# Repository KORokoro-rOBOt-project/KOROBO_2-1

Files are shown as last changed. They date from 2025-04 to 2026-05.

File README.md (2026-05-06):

# 〈第2.1世代〉ころボ / KOROBO (2.1 Gen)
> [!IMPORTANT]
> 組み立て説明を除き、他のデータは最低限完成しました！

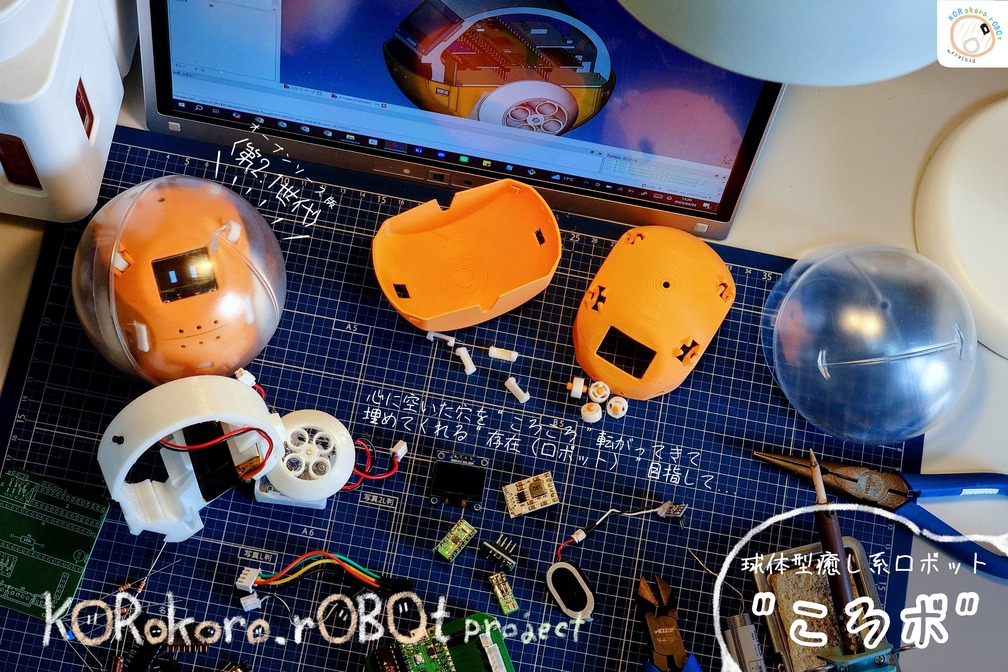
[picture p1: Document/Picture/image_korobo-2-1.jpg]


## 概要 / Overview
### ころボ？
“ころボ” は、カプセルに覆われた手のひらサイズのロボットです。
ただ、表情は四角い2つの瞳、動きはカプセル内で前後左右するも丸いカプセルに振り回され、言葉らしい言葉も話しません。

一見するとポンコツな子ですが、自身や周囲の状況に応じた繊細な反応、設計者の思惑を介さない不完全だからこそ引き出される解釈に、不思議と魅了されます。

そして、ロボットであることをさらけ出してはいるけれど、どこか私たちと同じ気配を感じる新たな存在になってほしいと考えています。

### 第2.1世代
〈第2.1世代〉ころボは、〈第2世代〉のオープンソース版として開発中の子です。
> 私のロボットに対する哲学や目指すべきコンセプトを、より明解にするためのプラットフォームとして考えています。その一方で、多くの方々にも ころボ で多種多様なアプローチをしていただけたらと思っている次第です。

<details>
<summary>第1世代、第2世代 / 1st Gen, 2nd Gen</summary>
	
<table>
  <thead>
    <tr>
      <th align="center"><strong>第1世代 / 1st Gen</strong></th>
      <th align="center"><strong>第2世代 / 2nd Gen</strong></th>
    </tr>
  </thead>
  <tbody>
    <tr>
      <td valign="top">
        〈第1世代〉ころボは、高専の本科生で最後となる高専祭に向けて制作された球体ロボットです。<br><br>
        <strong>直径8</strong> [<strong>cm</strong>]の小さなロボットは、特定の行動パターンを持たず、ランダムに転がります。
        そして、球体という不安定な要素と合わさり、あなたに自由な解釈でロボットと触れ合える余地（
        <a href="https://magazine.serviceology.org/2021/12/20/1433/" target="_blank"><strong>解釈の余地</strong></a>）を与えます。
      </td>
      <td valign="top">
        〈第2世代〉ころボは、
        <a href="https://hacku.yahoo.co.jp/kosen2021/" target="_blank">Hack U KOSEN 2021</a>
        に出場した際に制作した球体ロボットです。
        <strong>直径10</strong> [<strong>cm</strong>]の手にすっぽりおさまるロボットは、周囲の環境（
        <a href="https://twitter.com/KORokororOBOt/status/1652417063770820609" target="_blank"><strong>音</strong></a>、
        明るさ）や自身の状態（
        <a href="https://twitter.com/KORokororOBOt/status/1652271276403347457" target="_blank"><strong>加速度、角速度</strong></a>）を取得します。<br><br>
        それらの情報を反映させたことで、玩具っぽさが軽減され、あなたと同じ世界に住む存在なのだと感じられます。
        また、球体という不安定な要素と合わさり、あなたに自由な解釈でロボットと触れ合える余地（
        <a href="https://magazine.serviceology.org/2021/12/20/1433/" target="_blank"><strong>解釈の余地</strong></a>）を与えます。
      </td>
    </tr>
    <tr>
      <td valign="top">
        &emsp;&emsp;<strong>The first generation</strong> is a spherical robot I created as a department student for the Kosen College Festival.<br><br>
        &emsp;&emsp;The tiny robot, <strong>8 [cm]</strong> in diameter, has no specific action pattern and rolls randomly.
        Combined with the unstable element of the sphere, it gives you room to interact with the robot in any way you like (
        <a href="https://magazine.serviceology.org/2021/12/20/1433/" target="_blank"><strong>Room for Interpretation</strong></a>).
      </td>
      <td valign="top">
        &emsp;&emsp;<strong>The second generation</strong> is a spherical robot created for 
        <a href="https://hacku.yahoo.co.jp/kosen2021/" target="_blank">Hack U KOSEN 2021</a>.
        The <strong>10 [cm]</strong> diameter robot fits snugly in your hand and gets information about its surroundings (
        <a href="https://twitter.com/KORokororOBOt/status/1652417063770820609" target="_blank"><strong>Sound</strong></a>, Luminance) and its state (
        <a href="https://twitter.com/KORokororOBOt/status/1652271276403347457" target="_blank"><strong>Acceleration, Angular Velocity</strong></a>).<br><br>
        &emsp;&emsp;The robot reflects this information, making it feel less like a toy and more like a being that lives in the same world as you.
        Combined with the unstable element of the sphere, it gives you room to interact with the robot in any way you like (
        <a href="https://magazine.serviceology.org/2021/12/20/1433/" target="_blank"><strong>Room for Interpretation</strong></a>).
      </td>
    </tr>
  </tbody>
</table>

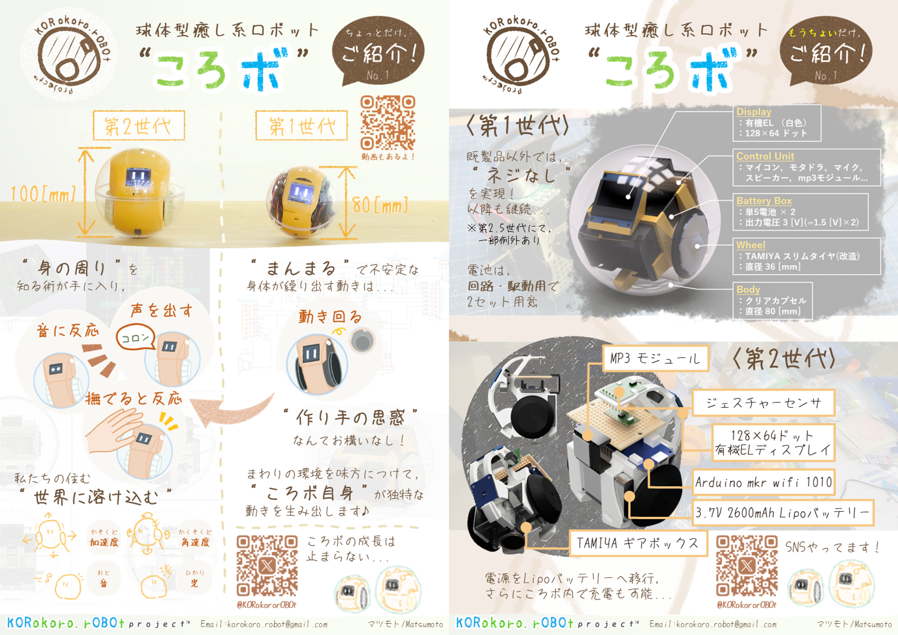
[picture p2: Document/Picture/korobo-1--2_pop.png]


</details>

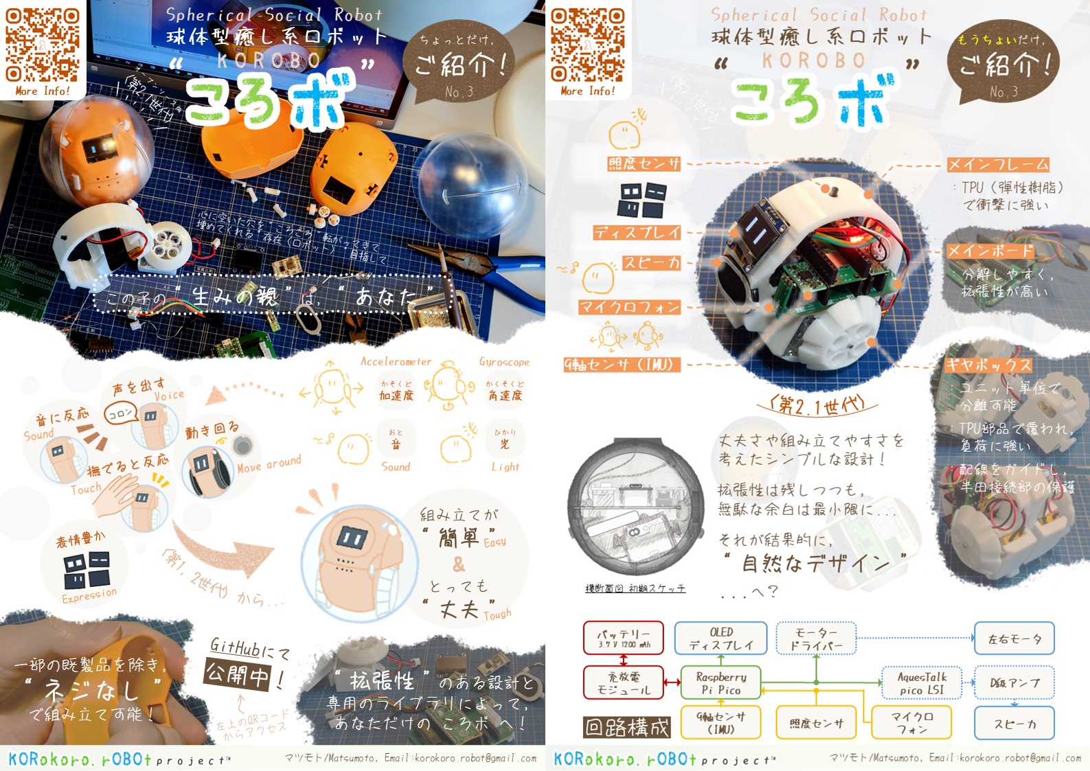
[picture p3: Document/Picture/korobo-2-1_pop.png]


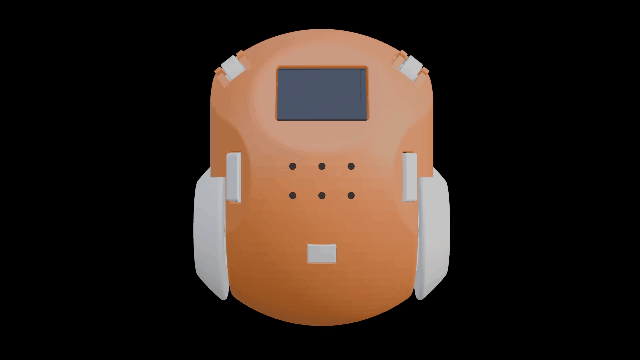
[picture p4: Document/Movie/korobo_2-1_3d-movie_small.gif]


- ころボ 開発当初から大切にしてきた**シンプルな構造**と、**はめ込みによる組み立て方式**[^1]はそのままに、**耐久性**や**拡張性**が向上しました！
    > 机から落ちても、間違えて蹴っ飛ばしても致命傷になることはありません。\
    > マイコンボードとアクセス可能なスペースがあり、思い思いに進化させられます。
[^1]: 既製品のギヤボックスキットは除く。

- マイコンボードに、Raspberry Pi Foundationが提供する[**Raspberry Pi Pico（ラズベリーパイピコ）**](https://www.raspberrypi.com/products/raspberry-pi-pico/)を採用しています！
    > 安価で入手性に優れ、様々な制作事例が存在します。\
    > 多くの互換ボードが存在し、USB端子や用途に合わせて自由に選べます。\
    > <a href="https://www.raspberrypi.com/products/raspberry-pi-pico-2/" >Raspberry Pi Pico 2</a>のように、世代が上がっても互換性があります。
 
## フォルダ構成 / Directory Layout
- [**Board**](Board): 基板発注に必要なガーバーデータ
- [**Code**](Code): ソースコード、ライブラリ
- [**Document**](Document): 調達リスト、画像など
- [**Model**](Model): STEPファイルおよびSTLファイル
## 組み立て / How to Set Up
<details open>
<summary><strong>目次</strong></summary>

0. [部品調達](#01-調達)
1. [駆動ユニット](#10-準備)
2. [配線](#20-準備)
3. [基板](#30-準備)
4. [はめ込み](#40-準備)
5. [ソースコード](#50-準備)
</details>

---
### 0. 部品調達（0/[1](#10-準備)/[2](#20-準備)/[3](#30-準備)/[4](#40-準備)/[5](#50-準備)）
#### 0.1 調達 
[Document](Document)に記載されている各種材料を、添付されているURLの通販サイトや実店舗などにて、調達してください。

#### 0.2 印刷
> [!TIP]
> KORokoro.rOBOt projectの[BOOTH](https://korokoro-robot.booth.pm/items/6812764)にて、**3Dプリンタ製部品**を調達された方は、"[0.3 基板発注 or 作成](#03-基板発注-or-作成)" へ進んでください。
<details>
<summary>手順</summary>

##### 0.20 準備
##### 0.21 PLA
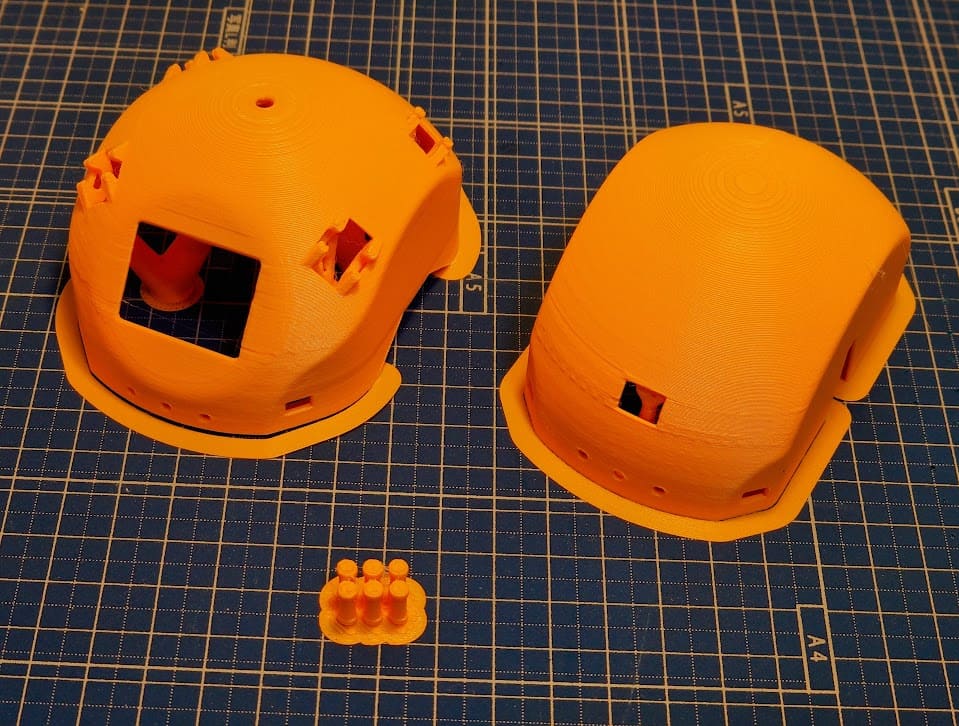
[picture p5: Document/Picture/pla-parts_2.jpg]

<p>
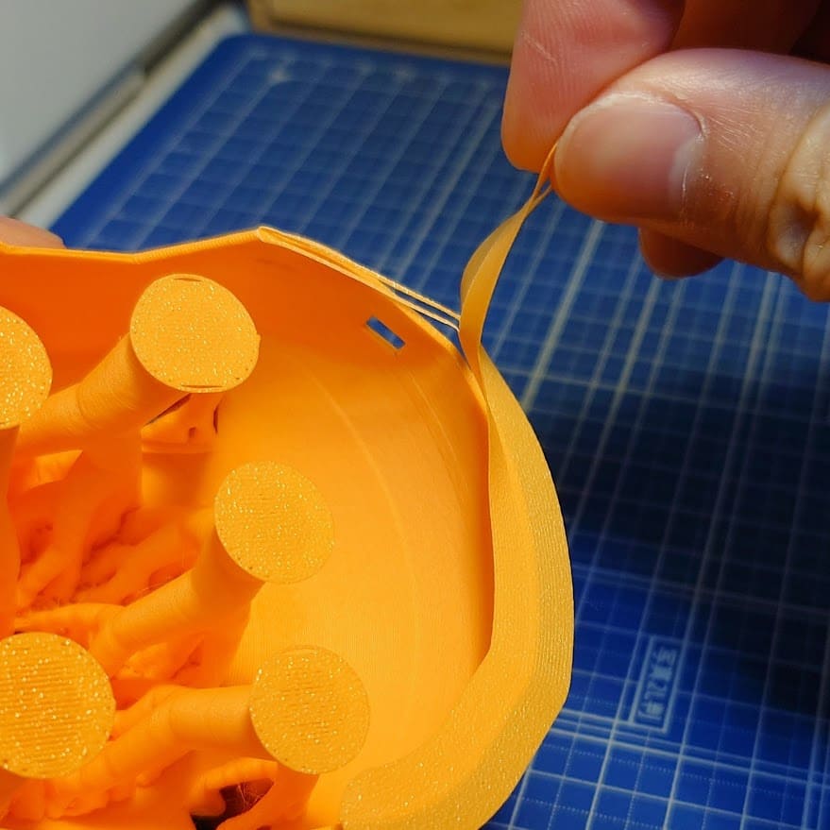
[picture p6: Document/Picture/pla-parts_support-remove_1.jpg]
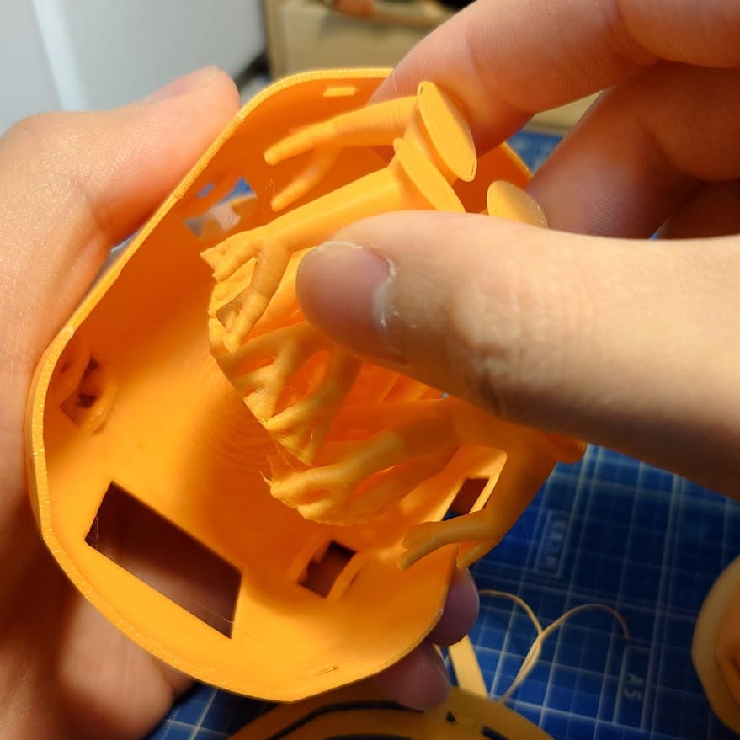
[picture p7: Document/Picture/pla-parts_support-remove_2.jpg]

</p>
<p>
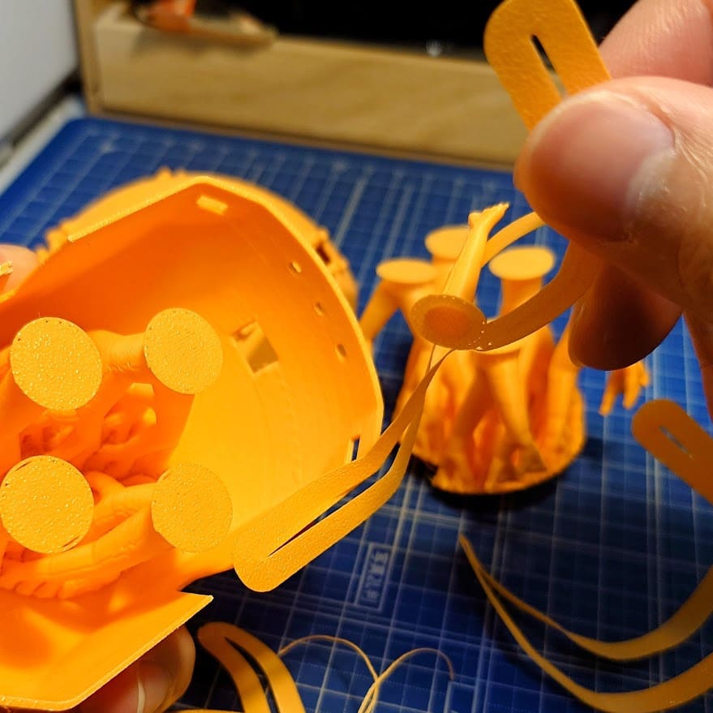
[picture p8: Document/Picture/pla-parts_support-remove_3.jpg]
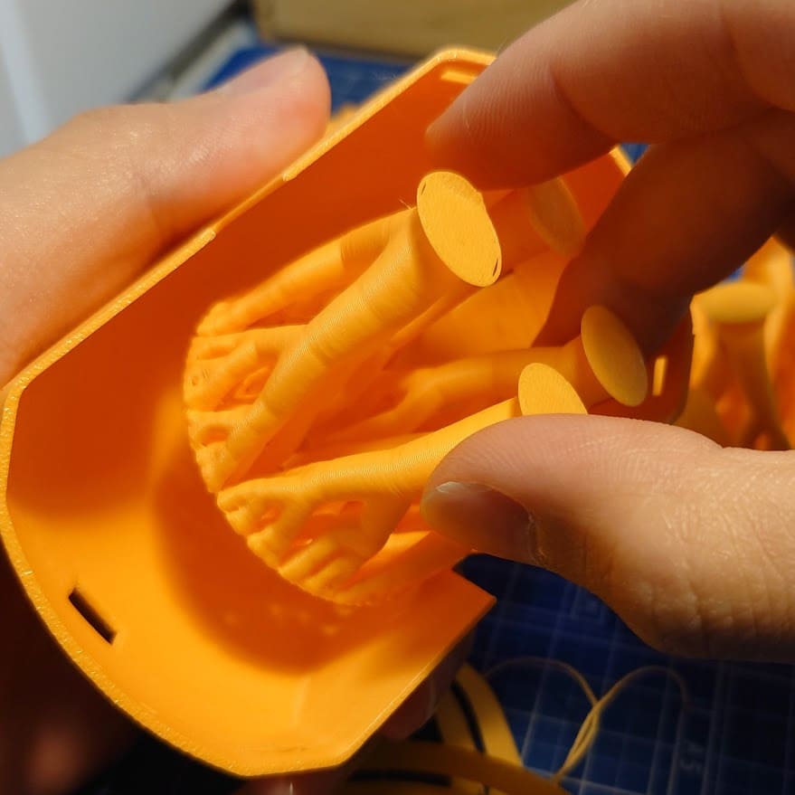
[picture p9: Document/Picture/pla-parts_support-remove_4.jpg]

</p>
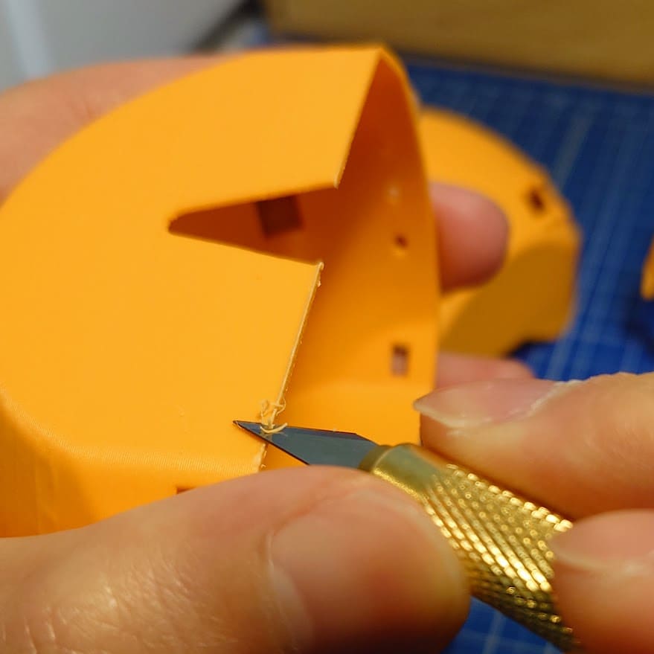
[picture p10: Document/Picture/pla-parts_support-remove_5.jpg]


##### 0.22 TPU
<p>
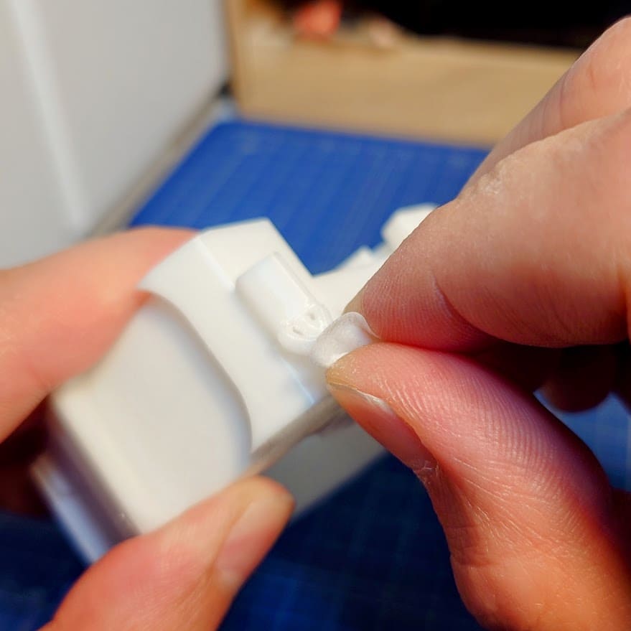
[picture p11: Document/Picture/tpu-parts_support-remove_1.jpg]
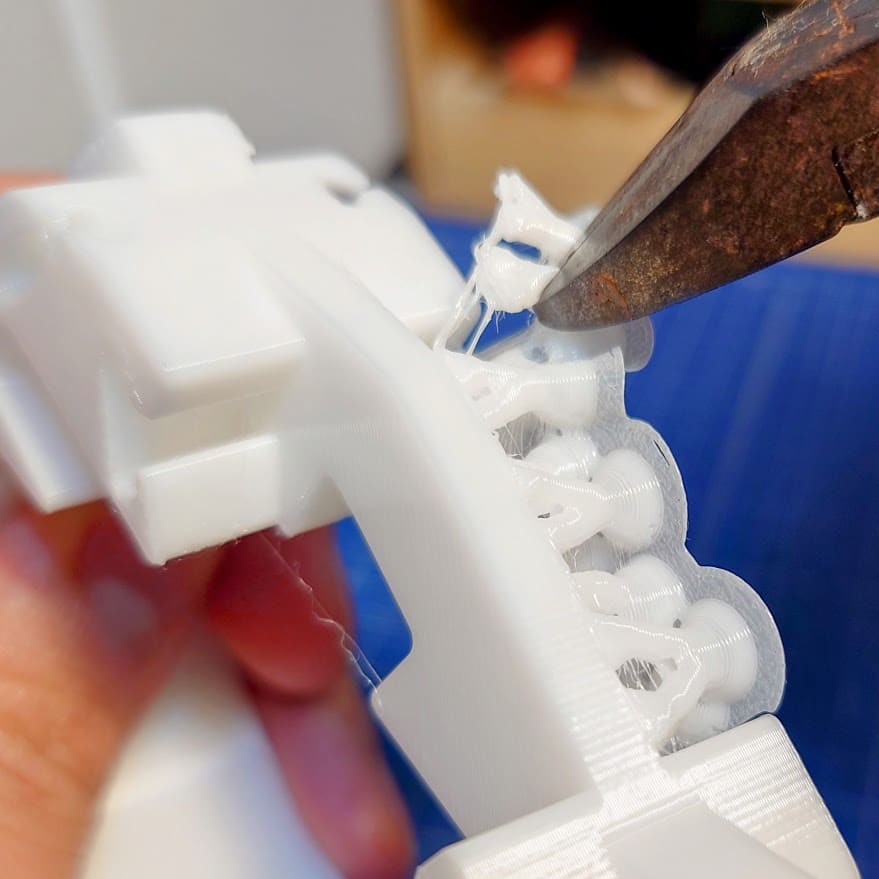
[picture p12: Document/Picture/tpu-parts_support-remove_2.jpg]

</p>
<p>
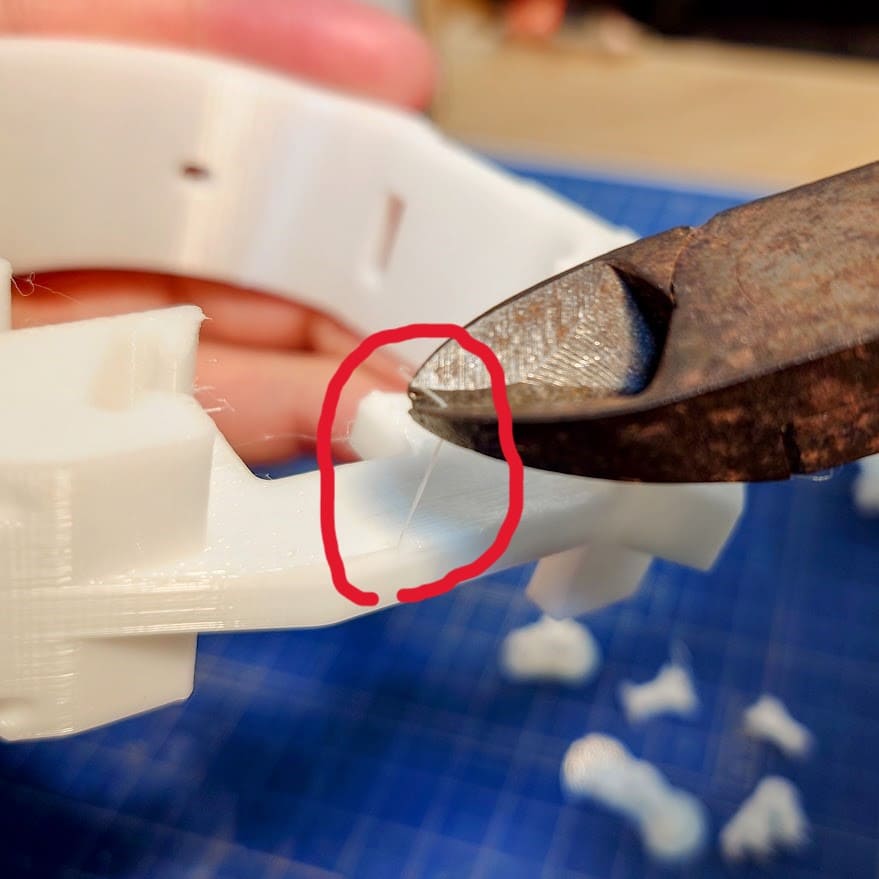
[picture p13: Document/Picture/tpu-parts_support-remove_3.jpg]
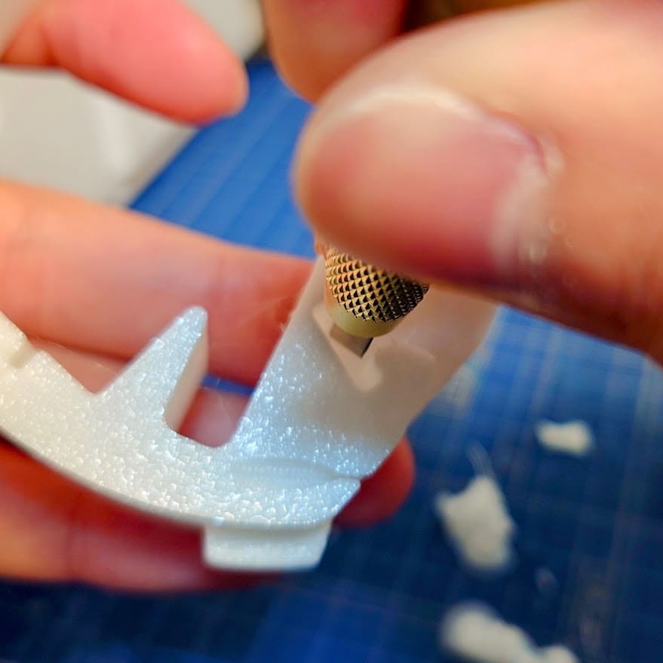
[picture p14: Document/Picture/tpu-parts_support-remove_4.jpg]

</p>
<p>
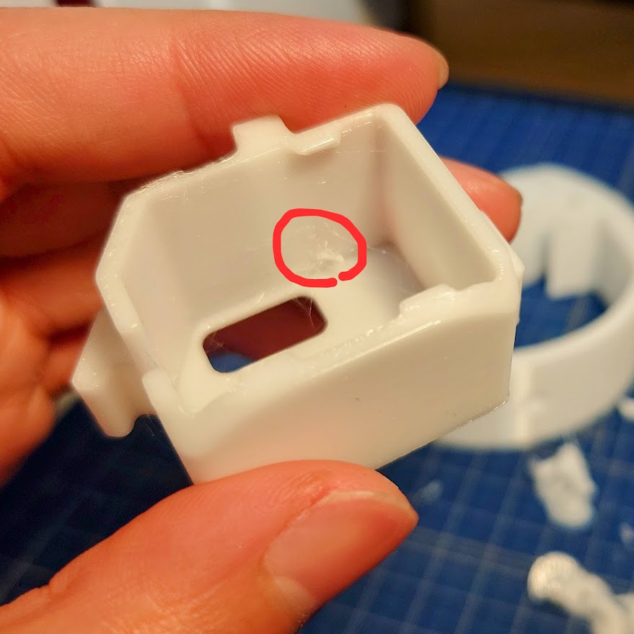
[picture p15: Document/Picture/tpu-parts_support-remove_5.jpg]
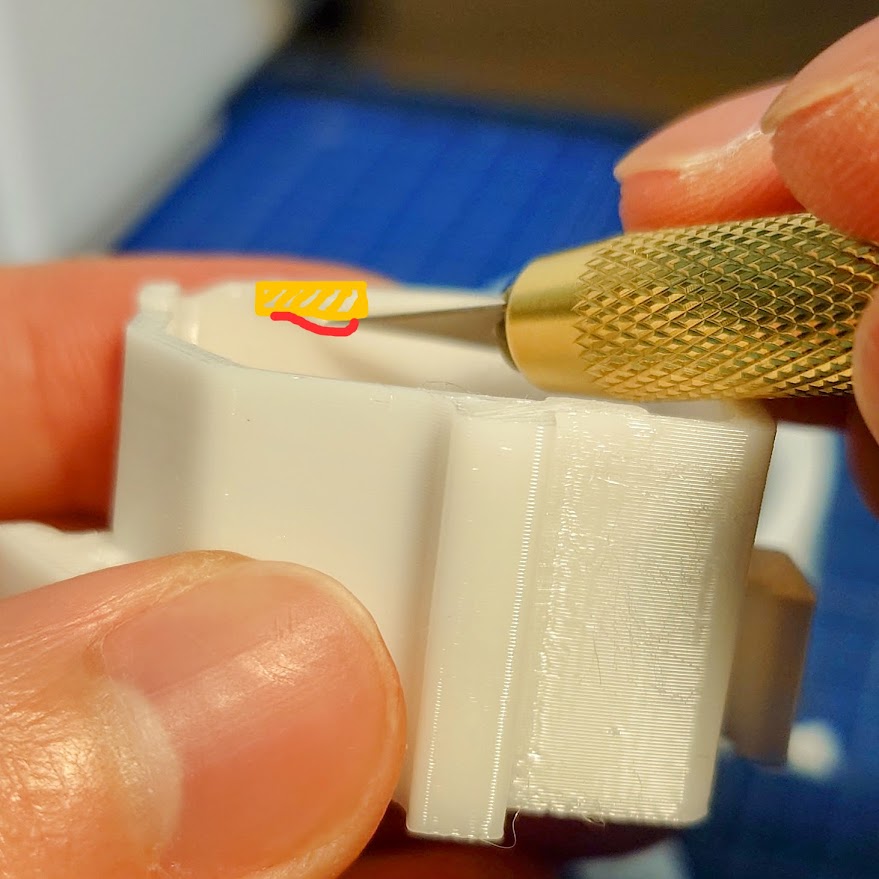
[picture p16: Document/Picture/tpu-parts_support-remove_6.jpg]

</p>
</details>

#### 0.3 基板発注 or 作成
> [!TIP]
> KORokoro.rOBOt projectの[BOOTH](https://korokoro-robot.booth.pm/items/6807081)にて、**メインボード**を調達された方は、"[1. 駆動ユニット](#10-準備)" へ進んでください。
<details open>
<summary>業者に発注される方</summary>

> [**Board**](Board)の中にあるzipファイルをPCBサイトへアップロードしてください。
</details>
<details>
<summary>ユニバーサル基板から作成される方（準備中）</summary>

準備中...
</details>

---
### 1. 駆動ユニット（[0](#01-調達)/1/[2](#20-準備)/[3](#30-準備)/[4](#40-準備)/[5](#50-準備)）
#### 1.0 準備
次の表に示す、工具・部品を準備してください。
<table>
  <thead>
    <tr>
      <th>項目</th>
      <th>名称</th>
      <th>個数</th>
    </tr>
  </thead>
  <tbody>
    <tr>
      <td rowspan="4">工具</td>
      <td>ニッパー</td>
      <td>1</td>
    </tr>
    <tr>
      <td>カッターナイフ or デザインナイフ</td>
      <td>1</td>
    </tr>
    <tr>
      <td>ピンセット</td>
      <td>1</td>
    </tr>
    <tr>
      <td>プラスドライバー</td>
      <td>1</td>
    </tr>
    <tr>
      <td rowspan="4">部品</td>
      <td>タミヤ ミニモーター低速ギヤボックス（4速）</td>
      <td>2</td>
    </tr>
    <tr>
      <td>タミヤ 3mm六角シャフトセット</td>
      <td>1</td>
    </tr>
    <tr>
      <td>メインタイヤ（3Dプリンタ製）</td>
      <td>2</td>
    </tr>
    <tr>
      <td>ギヤボックスカバー（3Dプリンタ製）</td>
      <td>2</td>
    </tr>
  </tbody>
</table>

#### 1.1 ギヤボックス
ミニモーター低速ギヤボックス（4速）を、付属の組み立て説明書に従って、組み立てます。

> [!NOTE]
> - ギヤ比は、"<b>149.9:1</b>" を使用します。
> - 六角シャフトは、3mm六角シャフトセットに付属する "<b>38 [mm]</b>" を使用します。
> - 付属説明書⑥の "<b>L2</b>"、⑦の "<b>クランクプレート</b>" は、使用しません。



#### 1.2 タイヤ＆カバー
> [!NOTE]
> 最後、カプセルに入れる際、圧入度合いの微調整をする必要があります。

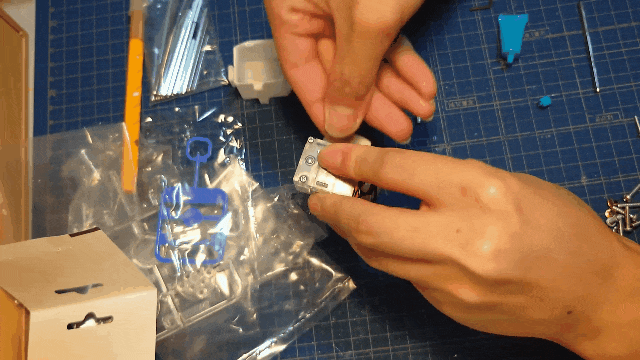
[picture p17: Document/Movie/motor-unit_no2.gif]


1. 調達したメインタイヤを、ギヤボックスのシャフトへ圧入します。

1. 調達したギヤボックスカバーを、ギヤボックスへはめ込みます。

---
### 2. 配線（[0](#01-調達)/[1](#10-準備)/2/[3](#30-準備)/[4](#40-準備)/[5](#50-準備)）
> [!TIP]
> KORokoro.rOBOt projectの[BOOTH](https://korokoro-robot.booth.pm/)にて、**配線類**を調達された方は、"[3. 基板](#30-準備)" へ進んでください。（※現在、準備中）

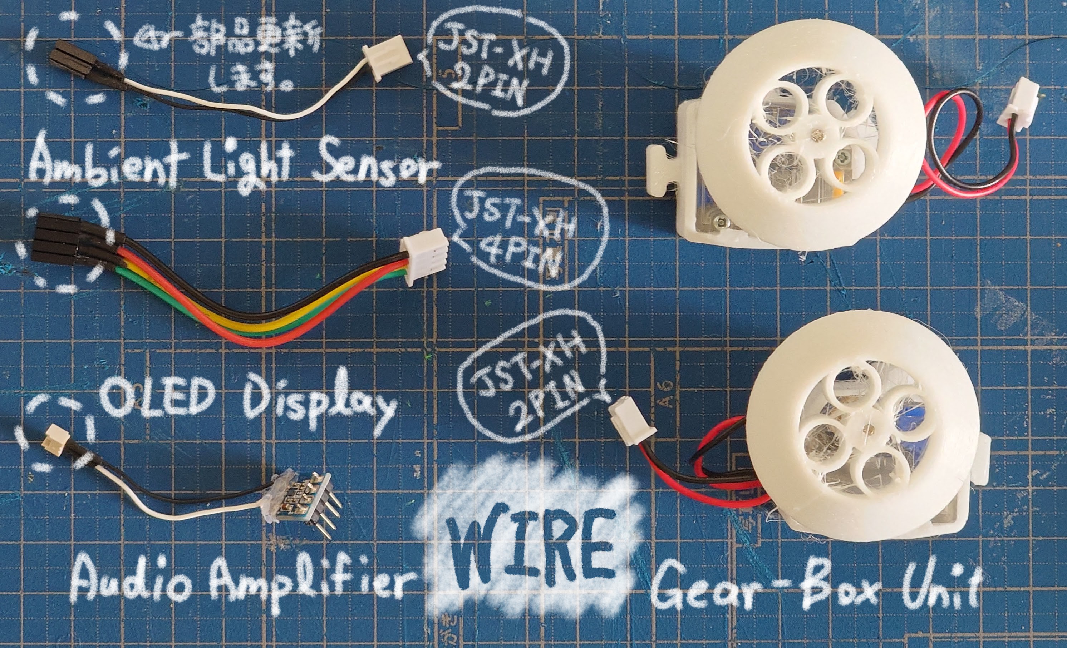
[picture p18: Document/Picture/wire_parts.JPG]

<details open>
<summary>手順</summary>

#### 2.0 準備
次の表に示す、工具・部品を準備してください。

<table>
	<thead>
		<tr>
			<th>項目</th>
			<th>名称</th>
		</tr>
	</thead>
	<tbody>
		<tr>
			<td rowspan="3">工具</td>
			<td>圧着工具</td>
		</tr>
		<tr>
			<td>グルーガン（+ グルースティック）</td>
		</tr>
		<tr>
			<td>ニッパー</td>
		</tr>
		<tr>
			<td rowspan="5">部品</td>
			<td>配線（赤, 黒, 他2色）</td>
		</tr>
		<tr>
			<td>ピンソケット（2P * 1, 4P * 1）</td>
		</tr>
		<tr>
			<td>JST-XH（2P * 3, 4P * 1）</td>
		</tr>
		<tr>
			<td>JST-PH（2P * 1）</td>
		</tr>
		<tr>
			<td>PicoBlade（2P * 1）</td>
		</tr>
	</tbody>
</table>

#### 2.1 駆動ユニット（JST-XH）
> モーター（2P）← 配線（黒、赤）→ JST-XH（2P）

#### 2.2 照度センサ（JST-XH, ピンソケット）
> JST-XH（2P）← 配線（黒、他色*1）→ ピンソケット（2P）

#### 2.3 ディスプレイ（JST-XH, ピンソケット）
> JST-XH（4P）← 配線（黒、赤、他色*2）→ ピンソケット（4P）



#### 2.4 スピーカー（PicoBlade）
> D級アンプ（2P）← 配線（黒、他色*1）→ PicoBlade（2P）

</details>

---
### 3. 基板（[0](#01-調達)/[1](#10-準備)/[2](#20-準備)/3/[4](#40-準備)/[5](#50-準備)）
#### 3.0 準備
次の表・画像に示す、工具・部品を準備してください。

<table>
  <thead>
    <tr>
      <th>項目</th>
      <th>名称</th>
    </tr>
  </thead>
  <tbody>
    <tr>
      <td rowspan="5">工具</td>
      <td>半田こて</td>
    </tr>
    <tr>
      <td>半田</td>
    </tr>
    <tr>
      <td>ニッパー</td>
    </tr>
    <tr>
      <td>机を保護できるマット</td>
    </tr>
    <tr>
      <td>基板や部品を固定できるモノ</td>
    </tr>
  </tbody>
</table>

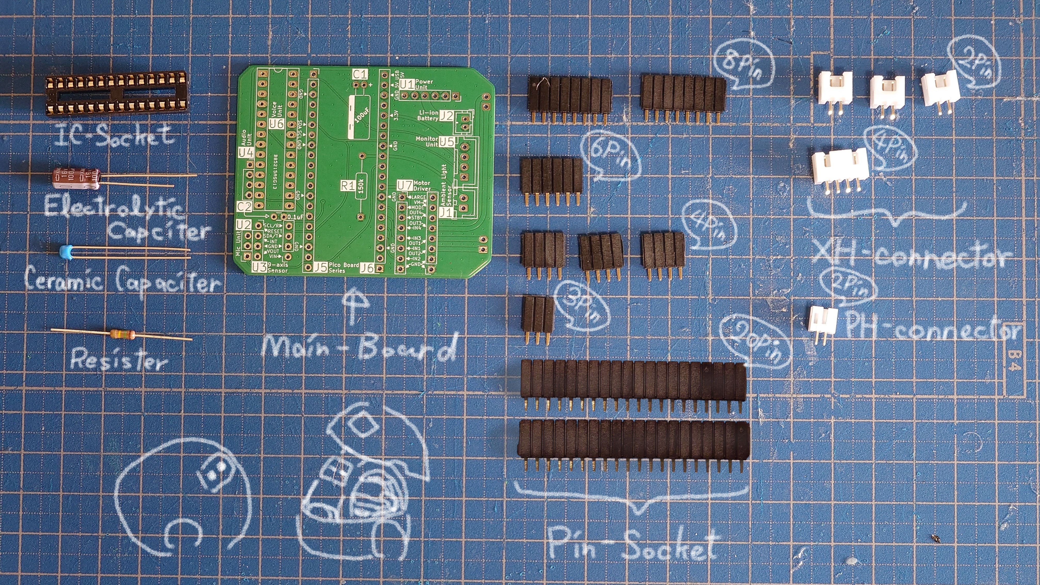
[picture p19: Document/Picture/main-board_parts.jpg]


#### 3.2 半田付け
> [!IMPORTANT]
> モジュール付属のピンヘッダーは、長さが異なるため、別途調達したピンヘッダーを推奨
1. **メインボード**
    > 作業過程ノーカット版 >> [クリック or タップ](https://youtu.be/Ys6NwztTmmA) \
    > 半田付け順：Resister/Capaciter → IC-Socket → XH/PH-Connecter → Pin-Socket

	準備中...
1. **モジュール**\
	準備中...

---
### 4. はめ込み（[0](#01-調達)/[1](#10-準備)/[2](#20-準備)/[3](#30-準備)/4/[5](#50-準備)）

#### 4.0 準備
次の表に示す、工具・部品を準備してください。

<table>
  <thead>
    <tr>
      <th>項目</th>
      <th>名称</th>
    </tr>
  </thead>
  <tbody>
    <tr>
      <td rowspan="3">工具</td>
      <td>やる気に満ちた手</td>
    </tr>
    <tr>
      <td>ビニールテープ</td>
    </tr>
    <tr>
      <td>ハサミ（テープを切断できるもの）</td>
    </tr>
    <tr>
      <td>部品</td>
      <td>これまで準備してきた部品すべて</td>
    </tr>
  </tbody>
</table>

#### 4.1 モジュール（順序あり）
> [!IMPORTANT]
> バッテリには、基板に近い部分をビニールテープなどで数回覆うことが推奨されます。

<div align="center">
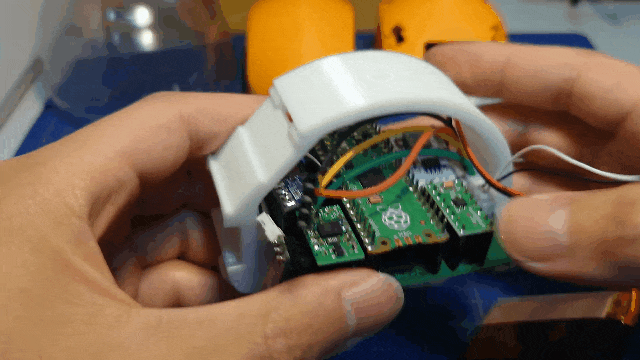
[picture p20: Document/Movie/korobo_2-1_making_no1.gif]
  
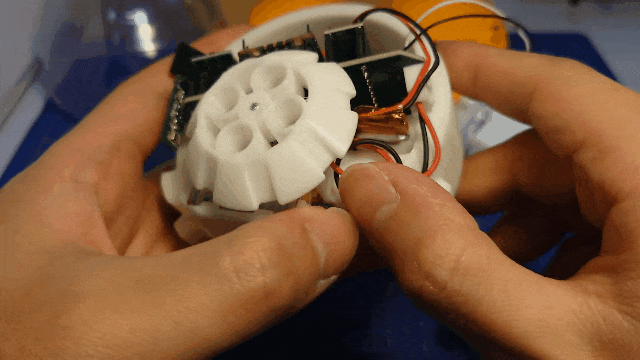
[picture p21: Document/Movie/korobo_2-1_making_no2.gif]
  
</div>

1. 基板 << 配線
1. メインフレーム << 基板（＋配線）
1. メインフレーム << バッテリ
1. メインフレーム << 駆動ユニット

#### 4.2 モジュール（順不同）
> [!NOTE]
> OLEDモジュールと接続するピンソケット（4P）は、接続向きに注意して下さい。GNDピンと黒線がペア！

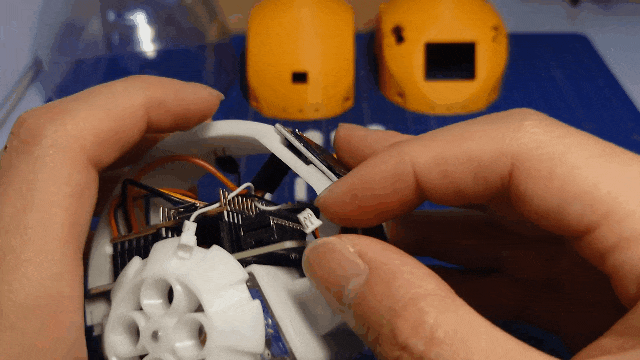
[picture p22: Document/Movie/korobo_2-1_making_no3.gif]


- メインフレーム << OLED、照度センサ、スピーカ

#### 4.3 カバー＆カプセル
<div align="center">
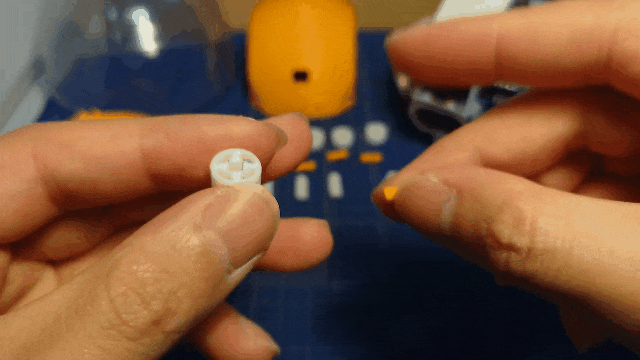
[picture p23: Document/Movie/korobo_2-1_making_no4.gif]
  
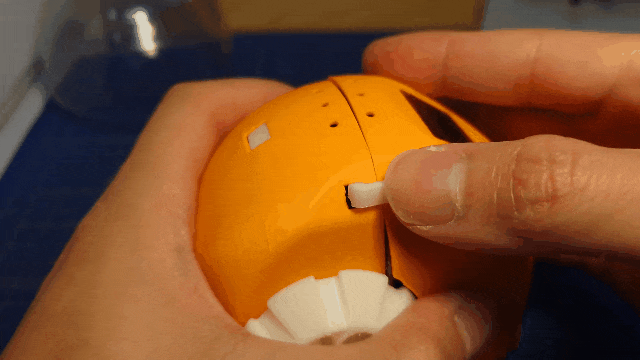
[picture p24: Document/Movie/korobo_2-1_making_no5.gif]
  
</div>

---
### 5. ソースコード（[0](#01-調達)/[1](#10-準備)/[2](#20-準備)/[3](#30-準備)/[4](#40-準備)/5）
#### 5.0 準備
次の表に示す、工具・部品を準備してください。

<table>
  <thead>
    <tr>
      <th>項目</th>
      <th>名称</th>
    </tr>
  </thead>
  <tbody>
    <tr>
      <td rowspan="2">工具</td>
      <td>USBケーブル</td>
    </tr>
    <tr>
      <td>PC</td>
    </tr>
    <tr>
      <td>部品</td>
      <td>ころボ の筐体</td>
    </tr>
  </tbody>
</table>

> [!NOTE]
> USBケーブルは、"PC" と "ころボのマイコンボード" に対応した規格（端子形状）を使用してください。

#### 5.1 配線
準備中...
#### 5.2 書き込み
準備中...
## ころボとの生活 / Life with KOROBO
#### 充電
ころボ の右側面にある、USB差込口に5V出力の**microUSB**を接続する。

#### その他
> [!CAUTION]
> - **リチウムイオン電池**を用いています。取り扱いにはご注意ください。
> - カプセルの仕様上、**完全防水ではありません**。
> - ころボ に関する問題は、自己責任でよろしくお願いいたします。

<p xmlns:cc="http://creativecommons.org/ns#" xmlns:dct="http://purl.org/dc/terms/"><a property="dct:title" rel="cc:attributionURL" href="https://github.com/KORokoro-rOBOt-project/KOROBO_2-1">〈第2.1世代〉ころボ</a> by <a rel="cc:attributionURL dct:creator" property="cc:attributionName" href="https://community.camp-fire.jp/projects/view/764851">KORokoro.rOBOt project</a> is licensed under <a href="https://creativecommons.org/licenses/by-sa/4.0/?ref=chooser-v1" target="_blank" rel="license noopener noreferrer" style="display:inline-block;">Creative Commons Attribution-ShareAlike 4.0 International</a></p>

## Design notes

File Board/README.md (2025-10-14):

# Board
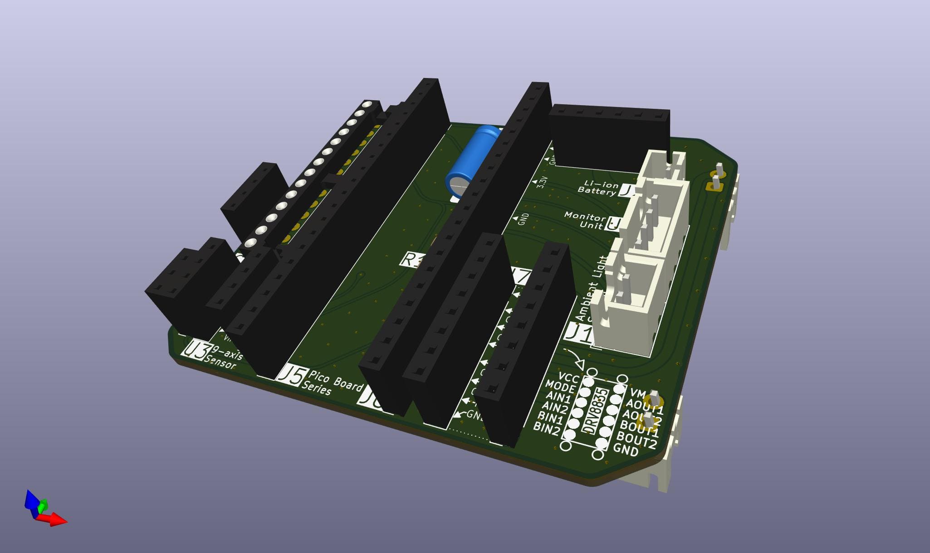
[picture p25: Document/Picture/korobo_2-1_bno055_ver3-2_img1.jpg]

<p>
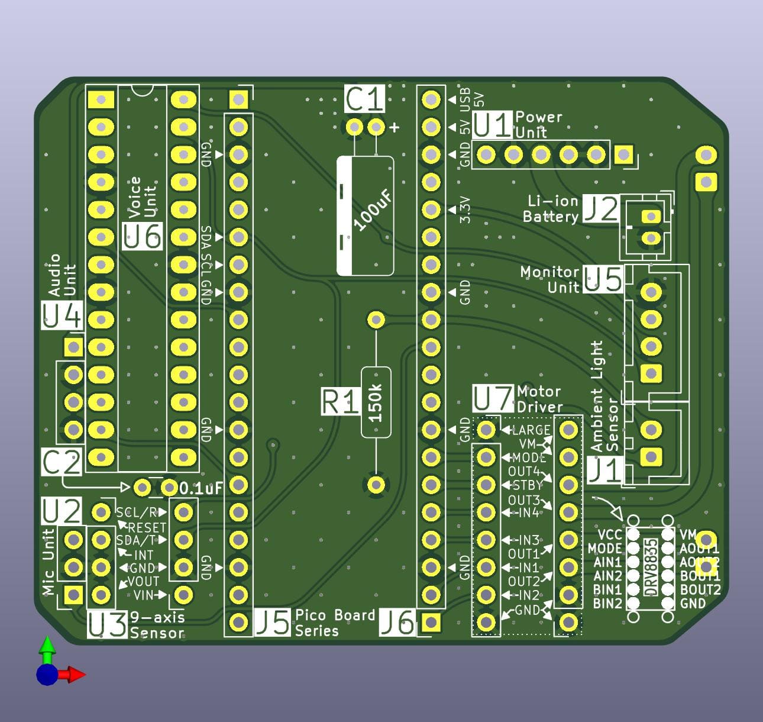
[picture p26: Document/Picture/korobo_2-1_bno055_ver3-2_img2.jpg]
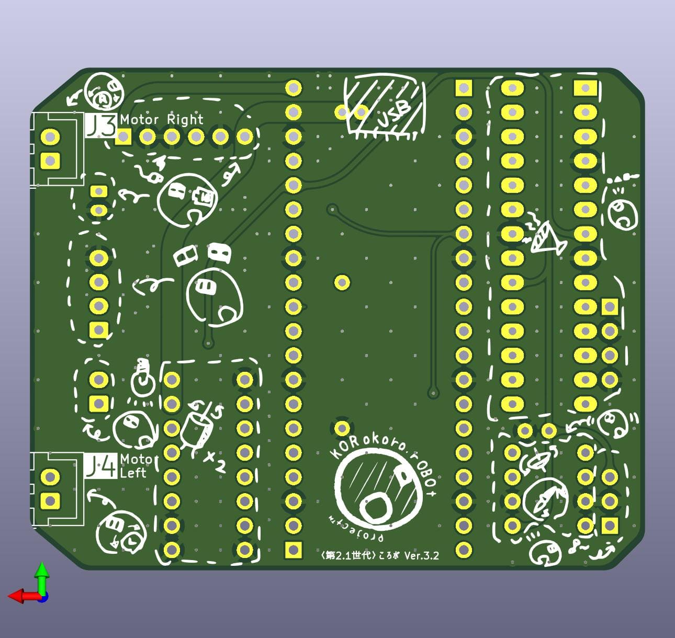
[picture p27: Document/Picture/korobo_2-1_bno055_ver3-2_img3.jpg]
  
</p>
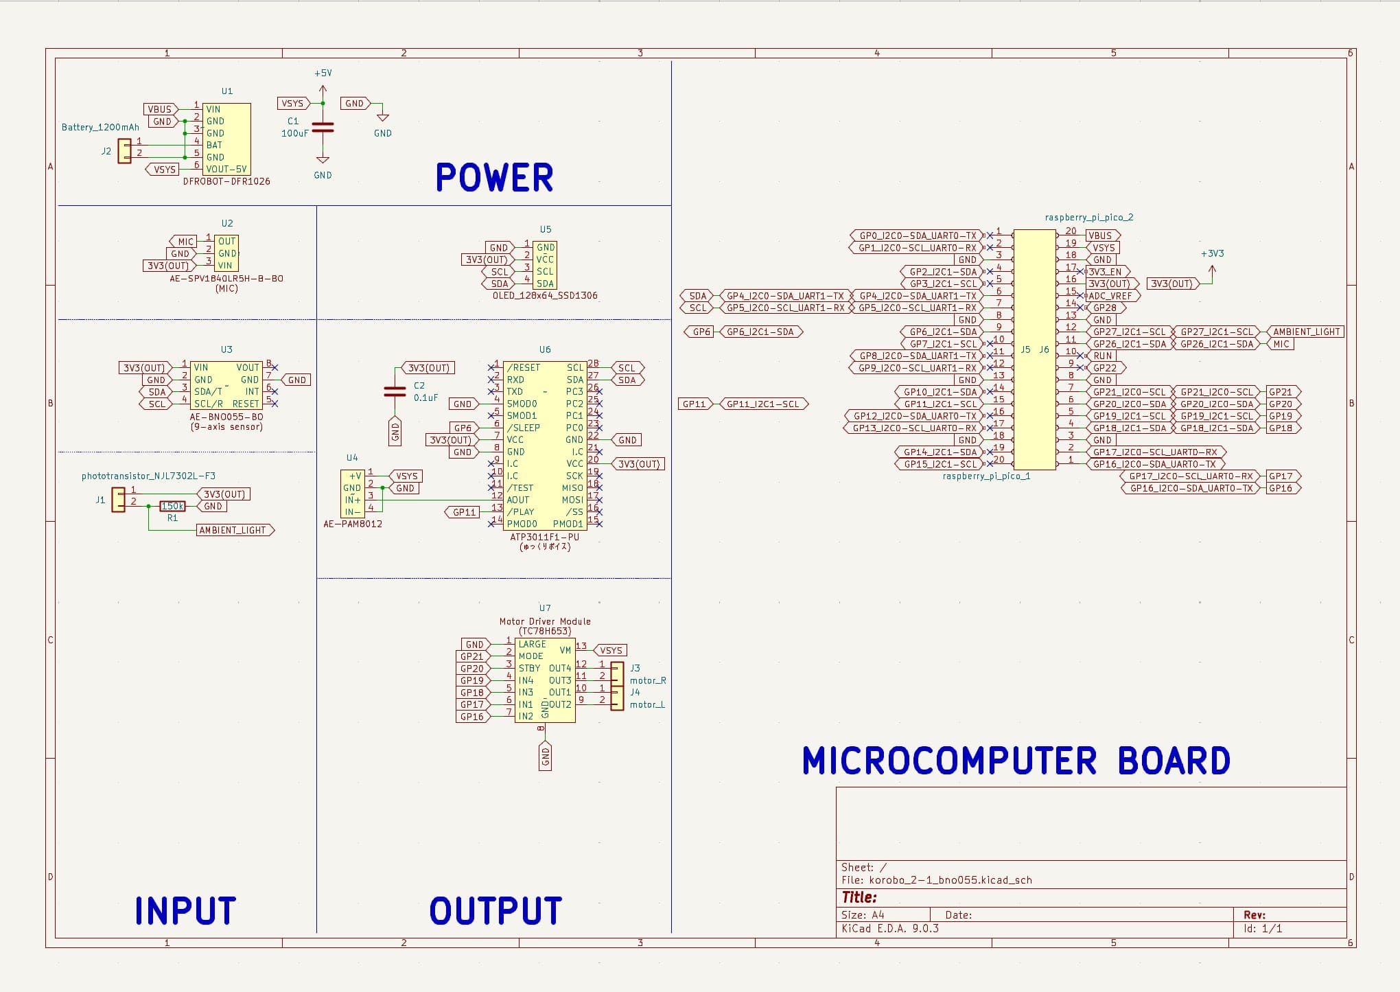
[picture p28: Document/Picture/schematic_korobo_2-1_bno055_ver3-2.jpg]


## 概要 / Overview
〈第2.1世代〉ころボのプリント基板は，組み立てやすさとメンテナンス性に注力しています．

- **ユニバーサル基板（2.54mm）との互換性**
  > プリント基板に設けられたスルーホールのピッチは，すべて2.54mmとなっています．
  > つまり，市販のユニバーサル基板との互換性があるため，プリント基板の調達が困難な方でも作成可能です（理論上...）．

- **ピンソケット・ヘッダーによる接続**
  > メインボードと各種モジュールは，ピンソケットとピンヘッダーによって接続されています．
  > そのため，簡単に取り外しでき，故障時の対応やマイコンボードの載せ替えが柔軟に行えます．

## 部品リスト / Parts List
| ラベル | 仕様 | 個数 | 補足 |
|:---:|---|:----:|---|
| C1 | 100uF | 1 | 電解コンデンサ |
| C2 | 0.1uF | 1 | セラミックコンデンサ |
| J1 | JST XH 2pin | 1 | 照度センサへ接続 |
| J2 | JST PH 2pin | 1 | バッテリへ接続 |
| J3 | JST XH 2pin | 1 | 右モータへ接続 |
| J4 | JST XH 2pin | 1 | 左モータへ接続 |
| J5 | PinSocket 2.54mm 20pin | 1 | マイコンボードへ接続 |
| J6 | PinSocket 2.54mm 20pin | 1 | マイコンボードへ接続 |
| R1 | 150k | 1 | 抵抗 |
| U1 | PinSocket 2.54mm 6pin | 1 | 充放電モジュールへ接続 |
| U2 | PinSocket 2.54mm 3pin | 1 | マイクセンサへ接続 |
| U3 | PinSocket 2.54mm 4pin | 2 | 9軸センサへ接続 |
| U4 | PinSocket 2.54mm 4pin | 1 | D級アンプへ接続 |
| U5 | JST XH 4pin | 1 | OLEDへ接続 |
| U6 | DIP-28 W7.62mm | 1 | ボイスICへ接続 |
| U7 | PinSocket 2.54mm 8pin | 2 | モータドライバへ接続 |



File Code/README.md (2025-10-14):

# Code
> [!NOTE]
> **Arduino IDE**を用いて，書き込みます．ボードマネージャーは，[**arduino-pico**](https://github.com/earlephilhower/arduino-pico)を利用します．

<details>
<summary>書き込み手順（準備中）</summary>
準備中．
</details>

## examples
### mind_2-1
〈第2.1世代〉ころボ の基本プログラム

  <details>
  <summary><ins>ソースコード</ins></summary>
    
  ```cpp
  #include "KoroboLib_2_1.h"
  
  KoroboLib_2_1 korobo;
  
  void setup() {
    // put your setup code here, to run once:
    Serial.begin(9600);
    korobo.begin(TC); // TC: TC78H653, DRV: DRV8833, OLD: main-board ver. 3.1
  }
  
  void loop() {
    // put your main code here, to run repeatedly:
    if (korobo.Sleep(ALL)) {
      korobo.Eye(ALL);
      korobo.Voice(ALL);
      korobo.Move();
    }
  }
  ```
  
  </details>

1. **ライブラリの読み込み**\
    `KoroboLib_2_1 korobo;`の`korobo`の部分は，任意の単語を指定可能．
   ただし，それ以降の`korobo.begin()`のような関数呼び出し時は，指定した単語に変更する必要がある．
    ```cpp
    #include "KoroboLib_2_1.h"
    
    KoroboLib_2_1 korobo;
    ```  
2. **初回処理**\
    
    `korobo.begin()`は，必須．
    ```cpp
    void setup() {
      // put your setup code here, to run once:
      Serial.begin(9600);
      korobo.begin(TC); // TC: TC78H653, DRV: DRV8833, OLD: main-board ver. 3.1
    }
    ```
3. **ループ処理**
    ```cpp
    void loop() {
      // put your main code here, to run repeatedly:
      if (korobo.Sleep(ALL)) {
        korobo.Eye(ALL);
        korobo.Voice(ALL);
        korobo.Move();
      }
    }
    ```

## KoroboLib_2_1
〈第2.1世代〉ころボ を動作させるにあたって必要となるライブラリ

> [!IMPORTANT]
> <b>KoroboLib_2_1</b>は，複数の既存ライブラリに依存しています．
> 事前に，それらのライブラリをインストールしてください[^1][^2][^3][^4]．
> また，各ライブラリには**異なるライセンス**が付与されています．
> これらのライブラリを独自に改変，または ころボ のライブラリへ組み込むといった場合は，十分にご確認ください．
[^1]: https://github.com/adafruit/Adafruit-GFX-Library
[^2]: https://github.com/adafruit/Adafruit_SSD1306
[^3]: https://github.com/adafruit/Adafruit_Sensor
[^4]: https://github.com/adafruit/Adafruit_BNO055

- **`void begin(unsigned int num)`** : 
各モジュールのセットアップ処理関数（[**mind_2-1** / 2. 初回処理](#begin)を参照）．
  > 引数に，搭載しているモータドライバの種類や，メインボードのバージョンを指定することで，互換性を確保している．
  <table>
    <thead>
      <tr>
        <th align="center">unsigned int num = </th>
        <th align="center">対応ボード・モータドライバ</th>
      </tr>
    </thead>
    <tbody>
      <tr>
        <td align="center"><code>TC</code></td>
        <td>メインボード Ver. 3.2，TC78H653 (= 1)</td>
      </tr>
      <tr>
        <td align="center"><code>DRV</code></td>
        <td>メインボード Ver. 3.2，DRV8833 (= 2)</td>
      </tr>
      <tr>
        <td align="center"><code>OLD</code></td>
        <td>メインボード Ver. 3.1，TC78H653 (= 0)</td>
      </tr>
    </tbody>
  </table>

- **`void Imu_getData()`** : 
記述した時点の9軸センサ（加速度・角速度・磁気）の値を取得できる．
  > 1回のループ処理中に複数実行しても，初めに実行した際の値が出力される．
  <table>
    <thead>
      <tr>
        <th align="center"><strong>変数</strong></th>
        <th align="center"><strong>内容</strong></th>
      </tr>
    </thead>
    <tbody>
      <tr>
        <td><code>korobo_acc.x()</code></td>
        <td>加速度（x軸）</td>
      </tr>
      <tr>
        <td><code>korobo_acc.y()</code></td>
        <td>加速度（y軸）</td>
      </tr>
      <tr>
        <td><code>korobo_acc.z()</code></td>
        <td>加速度（z軸）</td>
      </tr>
      <tr>
        <td><code>korobo_gyro.x()</code></td>
        <td>角速度（x軸）</td>
      </tr>
      <tr>
        <td><code>korobo_gyro.y()</code></td>
        <td>角速度（y軸）</td>
      </tr>
      <tr>
        <td><code>korobo_gyro.z()</code></td>
        <td>角速度（z軸）</td>
      </tr>
      <tr>
        <td><code>korobo_mag.x()</code></td>
        <td>磁気（x軸）</td>
      </tr>
      <tr>
        <td><code>korobo_mag.y()</code></td>
        <td>磁気（y軸）</td>
      </tr>
      <tr>
        <td><code>korobo_mag.z()</code></td>
        <td>磁気（z軸）</td>
      </tr>
    </tbody>
  </table>

    <details>
    <summary><ins>使用例</ins></summary>

    ```cpp
    void loop() {
      // put your main code here, to run repeatedly:
      float acc_x, acc_y, acc_z;
      korobo.Imu_getData();
      acc_x = korobo.korobo_acc.x();
      acc_y = korobo.korobo_acc.y();
      acc_z = korobo.korobo_acc.z();
    }
    ```
    </details>

- **`int AmbientLight_getData()`** :
上部光センサの値（0~1023）を取得できる．
- **`int Mic_getData()`** :
マイクセンサの値（0~1023）を取得できる．
- **`void Eye(3-pattern)`**
  
  - 
    ```cpp
    void Eye(unsigned int num)
    ```  
    > 瞳の表示および，瞳が表現する情報を選択できる．
  
    <table>
      <thead>
        <tr>
          <th align="center">unsigned int num = </th>
          <th align="center">内容</th>
        </tr>
      </thead>
      <tbody>
        <tr>
          <td align="center"><code>SOUND</code></td>
          <td>音情報を利用する (= 2)</td>
        </tr>
        <tr>
          <td align="center"><code>IMU</code></td>
          <td>加速度・角速度情報を利用する (= 3)</td>
        </tr>
        <tr>
          <td align="center"><code>LIGHT</code></td>
          <td>光情報を利用する (= 5)</td>
        </tr>
        <tr>
          <td align="center"><code>ALL</code></td>
          <td>すべての情報を利用する (= 30) <b>※推奨</b></td>
        </tr>
      </tbody>
    </table>
    
    <details>
    <summary><ins>使用例</ins></summary>

    ```cpp
    void loop() {
      // put your main code here, to run repeatedly:
      korobo.Eye(SOUND);        // 音情報のみ利用する．（1つの場合）
      korobo.Eye(IMU * LIGHT);  // 加速度・角速度および光情報を利用する．（複数の場合）
      korobo.Eye(ALL);          // すべての情報を利用する．
    }
    ```
    </details>
    
  - 
    ```cpp
    void Eye(int dX_point_u, int dY_point_u, int dX_size_u, int dY_size_u)
    ```
    > 瞳の表示および，瞳の各種パラメータのデフォルト値へ任意の操作を加えられる．
  
    <table>
      <thead>
        <tr>
          <th align="center">変数名</th>
          <th align="center">内容</th>
          <th align="center">値の範囲</th>
        </tr>
      </thead>
      <tbody>
        <tr>
          <td align="center"><code>int dX_point_u</code></td>
          <td>瞳のX座標</td>
          <td align="center">?~?</td>
        </tr>
        <tr>
          <td align="center"><code>int dY_point_u</code></td>
          <td>瞳のY座標</td>
          <td align="center">?~?</td>
        </tr>
        <tr>
          <td align="center"><code>int dX_size_u</code></td>
          <td>瞳の幅</td>
          <td align="center">?~?</td>
        </tr>
        <tr>
          <td align="center"><code>int dY_size_u</code></td>
          <td>瞳の高さ</td>
          <td align="center">?~?</td>
        </tr>
      </tbody>
    </table>
    
  -
    ```cpp
    void Eye(int dX_point_u, int dY_point_u, int dX_size_u, int dY_size_u, unsigned int num)
    ```
    > 上記，2項目の組み合わせ．

- **`void Motor(2-pattern)`** :
左右のモータに任意の操作量を加えられる．

  -
    ```cpp
    void Motor(int motor_power_l, int motor_power_r)
    ```
    > マイコンボードにUSB接続時は，モータ停止とする．<br>
    > 操作量が50以下のとき，ギヤボックスは出力が小さくカプセル内で止まってしまう．<br>
    > そのため，操作量が0~50のきとは，0と同じ扱いとしている．
    
    <table>
      <thead>
        <tr>
          <th align="center">変数</th>
          <th align="center">内容</th>
          <th align="center">値の範囲</th>
        </tr>
      </thead>
      <tbody>
        <tr>
          <td align="center"><code>int motor_power_l</code></td>
          <td>左モータの操作量</td>
          <td align="center">0 ~ 255</td>
        </tr>
        <tr>
          <td align="center"><code>int motor_power_r</code></td>
          <td>右モータの操作量</td>
          <td align="center">0 ~ 255</td>
        </tr>
      </tbody>
    </table>

  -
    ```cpp
    void Motor(int motor_power_l, int motor_power_r, bool flug)
    ```
    > `void Motor(int motor_power_l, int motor_power_r)`における，USB接続時のモータ停止を無効（`flug = false`）とする．

- **`void Move()`** : 
デフォルトの行動関数．
x, y軸の加速度を利用し，姿勢を水平な状態へ維持するようタイヤが動く．
  > この挙動とユーザーによる任意の操作を，同時行えるようにする予定．
- **`boolean Voice_state()`** : 
ころボが発話可能な状態か確認できる．
- **`void Voice_send(char Talk[20])`** : 
任意の文字列を発話できる．
文字列の文法は，[AquesTalk pico LSI](https://www.a-quest.com/products/aquestalkpicolsi.html)のデータシートを参照．
  > <code>Voice_state()</code>を内部に組み込んでいる．
- **`void Voice(unsigned int num)`** : 
デフォルトの発話関数．
発話が表現する情報を選択できる．
  <table>
    <thead>
      <tr>
        <th align="center">unsigned int num = </th>
        <th align="center">内容</th>
      </tr>
    </thead>
    <tbody>
      <tr>
        <td align="center"><code>SOUND</code></td>
        <td>音情報を利用する (= 2)</td>
      </tr>
      <tr>
        <td align="center"><code>IMU</code></td>
        <td>加速度・角速度情報を利用する (= 3)</td>
      </tr>
      <tr>
        <td align="center"><code>LIGHT</code></td>
        <td>光情報を利用する (= 5)</td>
      </tr>
      <tr>
        <td align="center"><code>ALL</code></td>
        <td>すべての情報を利用する (= 30) <b>※推奨</b></td>
      </tr>
    </tbody>
  </table>
  
    <details>
    <summary><ins>使用例</ins></summary>

    ```cpp
    void loop() {
      // put your main code here, to run repeatedly:
      korobo.Voice(SOUND);        // 音情報のみ利用する．（1つの場合）
      korobo.Voice(IMU * LIGHT);  // 加速度・角速度および光情報を利用する．（複数の場合）
      korobo.Voice(ALL);          // すべての情報を利用する．
    }
    ```
    </details>
    
- **（調整中）`boolean Sleep(unsigned int num)`** :
スリープ機能関数．
スリープへ移行する条件の情報を選択できる．
  <table>
    <thead>
      <tr>
        <th align="center">unsigned int num = </th>
        <th align="center">内容</th>
      </tr>
    </thead>
    <tbody>
      <tr>
        <td align="center"><code>SOUND</code></td>
        <td>音情報を利用する (= 2)</td>
      </tr>
      <tr>
        <td align="center"><code>IMU</code></td>
        <td>加速度・角速度情報を利用する (= 3)</td>
      </tr>
      <tr>
        <td align="center"><code>LIGHT</code></td>
        <td>光情報を利用する (= 5)</td>
      </tr>
      <tr>
        <td align="center"><code>ALL</code></td>
        <td>すべての情報を利用する (= 30) <b>※推奨</b></td>
      </tr>
    </tbody>
  </table>
  
    <details>
    <summary><ins>使用例</ins></summary>

    ```cpp
    void loop() {
      // put your main code here, to run repeatedly:
      // 例：Sleep(SOUND), Sleep(IMU * LIGHT)...
      if (korobo.Sleep(ALL)) {
        /* スリープ中に行わない処理... */
      }
      /* スリープ中にも行う処理... */
    }
    ```
    </details>

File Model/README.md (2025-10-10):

# Model
## STL & STEP
> [!NOTE]
> **STEP形式**を推奨しています．

| ファイル名 | 説明 | 印刷数 | 素材 |
|---|---|:---:|:----:|
| [**cover_b_2-1.stl**](STL(OLD)/cover_b_2-1.stl)<br>[**cover_b_2-1.step**](STEP/cover_b_2-1.step) | 本体カバーの下部 | 1 | PLA |
| [**cover_stopper.stl**](STL(OLD)/cover_stopper.stl)<br>[**cover_stopper.step**](STEP/cover_stopper.step) | 本体カバーの上部と下部を繋げるアタッチメント | 4 | TPU |
| [**cover_t_2-1.stl**](STL(OLD)/cover_t_2-1.stl)<br>[**cover_t_2-1.step**](STEP/cover_t_2-1.step.step) | 本体カバーの上部 | 1 | PLA |
| [**main_frame_2-1.stl**](STL(OLD)/main_frame_2-1.stl)<br>[**main_frame_2-1.step**](STEP/main_frame_2-1.step) | メインフレーム | 1 | TPU |
| [**motor_frame_2-1.stl**](STL(OLD)/motor_frame_2-1.stl)<br>[**motor_frame_2-1.step**](STEP/motor_frame_2-1.step) | ギアボックスを包むカバー | 2[^1] | TPU |
| [**wheel_b_2-1.stl**](STL(OLD)/wheel_b_2-1.stl)<br>[**wheel_b_2-1.step**](STEP/wheel_b_2-1.step) | メインタイヤ | 2 | TPU |
| [**wheel_t.stl**](STL(OLD)/wheel_t.stl)<br>[**wheel_t.step**](STEP/wheel_t.step) | 上部滑車 | 4 | TPU |
| [**wheel_t_shaft.stl**](STL(OLD)/wheel_t_shaft.stl)<br>[**wheel_t_shaft.step**](STEP/wheel_t_shaft.step) | 上部滑車の軸 | 4 | PLA |

[^1]: `motor_frame_2-1`は，左右対称で1個ずつ計2個を印刷．

## 2-1Gen_KOROBO.step
各種部品の位置関係などが確認できます．

> [!IMPORTANT]
> 内部データの一部は，[**GRABCAD COMMUNITY**](https://grabcad.com/library)に参加する有志の方々からお借りています[^2][^3]．

[^2]: Raspberry Pi Pico >> https://grabcad.com/library/raspberry-pi-pico-3 
[^3]: Atmega328 >> https://grabcad.com/library/atmega328-1

## korobo_2-1_PLA.3mf & korobo_2-1_TPU.3mf
スライサソフト**Bambu Studio**にて編集したプロジェクトファイルです（設定プリンタ：A1 mini）．

Bambu Lab製品をお持ちの方でしたら，お持ちのプリンタ・フィラメントを選択し，スライスしていただけたらと思います．

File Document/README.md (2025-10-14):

# Document
## [調達リスト / Parts List](Parts-List_KOROBO_2-1.pdf) (2025/9/23)
> [!TIP]
> **電子工作をされている方**は，手元にある部品を確認することで，調達コストを抑えられる場合があります．<br>
> （例：ピンソケット，ピンヘッダ，抵抗，コンデンサなど）

> [!NOTE]
> 一部の部品にて，**組み立てサポート品**を販売しています．<br>
> 「3Dプリンタが家にない」，「基板発注の経験がない」といった方々でも，ころボ に触れ合っていただけます！\
> [▼ 紹介動画（クリック or タップ）](https://www.youtube.com/watch?v=OCpZHEYD810)\
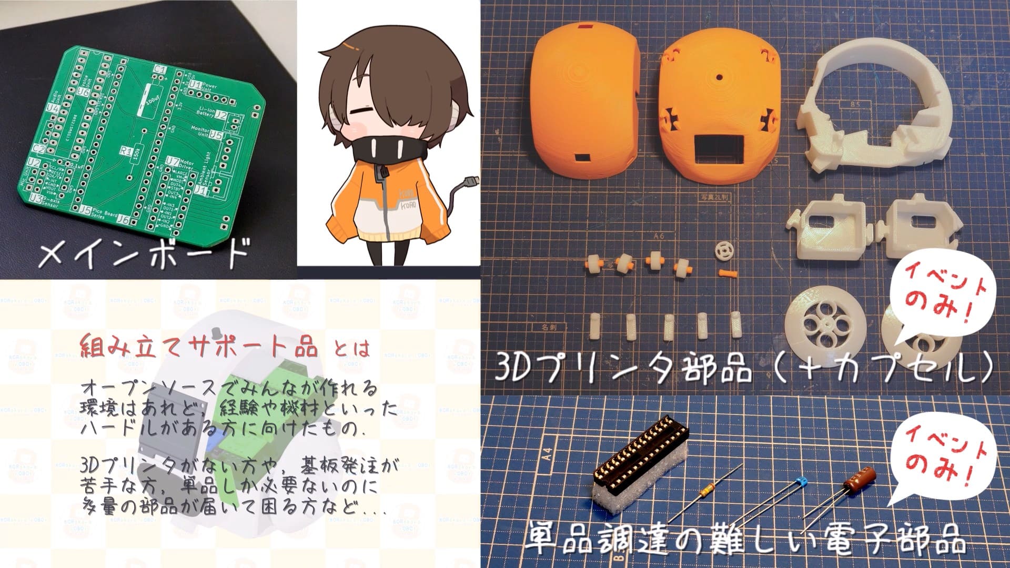
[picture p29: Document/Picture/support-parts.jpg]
> 

> Amazonの商品URLについては，Amazonアソシエイトの短縮リンクを使用しています．<br>
> ※Amazonのアソシエイトとして、KORokoro.rOBOt projectは適格販売により収入を得ています．

### 一覧表示 / All
<details>
<summary>表示 / Preview</summary>
<table>
  <tr>
    <th style="text-align:center;" rowspan="2">No.</th>
    <th style="text-align:center;" rowspan="2">品名</th>
    <th style="text-align:center;">単価</th>
    <th style="text-align:center;" rowspan="2">個数</th>
    <th style="text-align:center;">小計</th>
    <th style="text-align:center;" colspan="2">調達先</th>
    <th style="text-align:center;" rowspan="2">備考</th>
  </tr>
  <tr>
    <th style="text-align:center;">a</th>
    <th style="text-align:center;">a</th>
    <th style="text-align:center;">a</th>
    <th style="text-align:center;">b</th>
  </tr>
  <tr>
    <td colspan="8" align="center">
      <ins>秋月電子</ins>
    </td>
  </tr>
  <tr>
    <td>1</td>
    <td>Raspberry Pi Pico</td>
    <td>¥770</td>
    <td>1</td>
    <td>¥770</td>
    <td><a href="https://akizukidenshi.com/catalog/g/g116132/">秋月電子</a></td>
    <td><a href="https://ssci.to/6900">SWITCH<br>SCIENCE</a></td>
    <td></td>
  </tr>
  <tr>
    <td>2</td>
    <td>0.96インチ 128×64ドット<br>有機ELディスプレイ(OLED) 白色</td>
    <td>¥580</td>
    <td>1</td>
    <td>¥580</td>
    <td><a href="https://akizukidenshi.com/catalog/g/g112031/">秋月電子</a></td>
    <td></td>
    <td></td>
  </tr>
  <tr>
    <td>3</td>
    <td>BNO055使用 9軸センサー<br>フュージョンモジュールキット</td>
    <td>¥2,450</td>
    <td>1</td>
    <td>¥2,450</td>
    <td><a href="https://akizukidenshi.com/catalog/g/g116996/">秋月電子</a></td>
    <td></td>
    <td></td>
  </tr>
  <tr>
    <td>4</td>
    <td>SPV1840LR5H-B使用<br>シリコンマイクモジュールキット</td>
    <td>¥450</td>
    <td>1</td>
    <td>¥450</td>
    <td><a href="https://akizukidenshi.com/catalog/g/g116573/">秋月電子</a></td>
    <td></td>
    <td></td>
  </tr>
  <tr>
    <td>5</td>
    <td>TC78H653FTG<br>モータードライバーモジュール</td>
    <td>¥200</td>
    <td>1</td>
    <td>¥200</td>
    <td><a href="https://akizukidenshi.com/catalog/g/g114746/">秋月電子</a></td>
    <td></td>
    <td></td>
  </tr>
  <tr>
    <td>6</td>
    <td>音声合成LSI ATP3011F1-PU<br>(ゆっくりな女性の音声)</td>
    <td>¥1,050</td>
    <td>1</td>
    <td>¥1,050</td>
    <td><a href="https://akizukidenshi.com/catalog/g/g106220/">秋月電子</a></td>
    <td></td>
    <td></td>
  </tr>
  <tr>
    <td>7</td>
    <td>PAM8012使用2ワット<br>D級アンプモジュール</td>
    <td>¥300</td>
    <td>1</td>
    <td>¥300</td>
    <td><a href="https://akizukidenshi.com/catalog/g/g108217/">秋月電子</a></td>
    <td></td>
    <td></td>
  </tr>
  <tr>
    <td>8</td>
    <td>照度センサー<br>NJL7302L-F3</td>
    <td>¥45</td>
    <td>1</td>
    <td>¥45</td>
    <td><a href="https://akizukidenshi.com/catalog/g/g108910/">秋月電子</a></td>
    <td></td>
    <td></td>
  </tr>
  <tr>
    <td>9</td>
    <td>カーボン抵抗 1/2W150kΩ</td>
    <td>¥100</td>
    <td>1</td>
    <td>¥100</td>
    <td><a href="https://akizukidenshi.com/catalog/g/g107855/">秋月電子</a></td>
    <td></td>
    <td></td>
  </tr>
  <tr>
    <td>10</td>
    <td>積層セラミックコンデンサー<br>0.1μF50V X7R 2.54mm 10個</td>
    <td>¥100</td>
    <td>1</td>
    <td>¥100</td>
    <td><a href="https://akizukidenshi.com/catalog/g/g113582/">秋月電子</a></td>
    <td></td>
    <td></td>
  </tr>
  <tr>
    <td>11</td>
    <td>電解コンデンサー100μ<br>F25V105℃ ルビコンPX</td>
    <td>¥10</td>
    <td>1</td>
    <td>¥10</td>
    <td><a href="https://akizukidenshi.com/catalog/g/g117877/">秋月電子</a></td>
    <td></td>
    <td></td>
  </tr>
  <tr>
    <td>12</td>
    <td>分割ロングピンソケット 1×42 (42P)</td>
    <td>¥80</td>
    <td>3</td>
    <td>¥240</td>
    <td><a href="https://akizukidenshi.com/catalog/g/g105779/">秋月電子</a></td>
    <td></td>
    <td></td>
  </tr>
  <tr>
    <td>13</td>
    <td>ピンヘッダー 1×40 (40P)</td>
    <td>¥35</td>
    <td>3</td>
    <td>¥105</td>
    <td><a href="https://akizukidenshi.com/catalog/g/g100167/">秋月電子</a></td>
    <td></td>
    <td></td>
  </tr>
  <tr>
    <td>14</td>
    <td>ピンソケット 1×20 (20P)<br>リード長10mm</td>
    <td>¥60</td>
    <td>2</td>
    <td>¥120</td>
    <td><a href="https://akizukidenshi.com/catalog/g/g118376/">秋月電子</a></td>
    <td><a href="https://ssci.to/8027">SWITCH<br>SCIENCE</a></td>
    <td></td>
  </tr>
  <tr>
    <td>15</td>
    <td>コネクター用ハウジング 2P</td>
    <td>¥10</td>
    <td>1</td>
    <td>¥10</td>
    <td><a href="https://akizukidenshi.com/catalog/g/g112151">秋月電子</a></td>
    <td></td>
    <td></td>
  </tr>
  <tr>
    <td>16</td>
    <td>コネクター用ハウジング 4P</td>
    <td>&yen;10</td>
    <td>1</td>
    <td>&yen;10</td>
    <td><a href="https://akizukidenshi.com/catalog/g/g112153/">秋月電子</a></td>
    <td><u></u></td>
    <td rowspan="2">
      ピンソケットでも対応できます．<br>
      ▼コネクター側だけ利用する手法もあります．<br>
      <a href="https://eleshop.jp/shop/g/gAAC41C/?srsltid=AfmBOoqFBb0585i-U3NJiWO_EpqYxHgdgGQ-2iUeOSxdOJOnOQ2duirH0ts">共立エレショップ</a>
    </td>
  </tr>
  <tr>
    <td>17</td>
    <td>ケーブル用コネクター 10個</td>
    <td>&yen;50</td>
    <td>1</td>
    <td>&yen;50</td>
    <td><a href="https://akizukidenshi.com/catalog/g/g112160">秋月電子</a></td>
    <td><u></u></td>
    <!-- 備考セルは上の行と結合しているため省略 -->
  </tr>
  <tr>
    <td>18</td>
    <td>ICソケット (28P) スリム300milタイプ</td>
    <td>&yen;280</td>
    <td>1</td>
    <td>&yen;280</td>
    <td><a href="https://akizukidenshi.com/catalog/g/g100013/">秋月電子</a></td>
    <td></td>
    <td></td>
  </tr>
  <tr>
    <td>19</td>
    <td>PHコネクター ベース付ポスト<br>トップ型 2P B2B-PH-K-S</td>
    <td>&yen;10</td>
    <td>1</td>
    <td>&yen;10</td>
    <td><a href="https://akizukidenshi.com/catalog/g/g112802/">秋月電子</a></td>
    <td><a href="https://amzn.to/4nIFLoP">Amazon</a></td>
    <td rowspan="6">候補2のAmazonから調達したほうが，部品を紛失してもある程度予備を確保しつつ，専用ケースで保管できるため，扱いやすいかもです．</td>
  </tr>
  <tr>
    <td>20</td>
    <td>XHコネクター ベース付ポスト<br>トップ型 2P B2B-XH-A(LF)(SN)</td>
    <td>&yen;10</td>
    <td>3</td>
    <td>&yen;30</td>
    <td><a href="https://akizukidenshi.com/catalog/g/g112247/">秋月電子</a></td>
    <td rowspan="5"><a href="https://amzn.to/42ELjbL">Amazon</a></td>
  </tr>
  <tr>
    <td>21</td>
    <td>XHコネクター ベース付ポスト<br>トップ型 4P B4B-XH-A(LF)(SN)</td>
    <td>&yen;10</td>
    <td>1</td>
    <td>&yen;10</td>
    <td><a href="https://akizukidenshi.com/catalog/g/g112249/">秋月電子</a></td>
  </tr>
  <tr>
    <td>22</td>
    <td>XHコネクター ハウジング用コンタクト<br>SXH-001T-P0.6</td>
    <td>&yen;200</td>
    <td>1</td>
    <td>&yen;200</td>
    <td><a href="https://akizukidenshi.com/catalog/g/g112265/">秋月電子</a></td>
  </tr>
  <tr>
    <td>23</td>
    <td>XHコネクター ハウジング 4P XHP-4</td>
    <td>&yen;5</td>
    <td>1</td>
    <td>&yen;5</td>
    <td><a href="https://akizukidenshi.com/catalog/g/g112257/">秋月電子</a></td>
  </tr>
  <tr>
    <td>24</td>
    <td>XHコネクター ハウジング 2P XHP-2</td>
    <td>&yen;5</td>
    <td>3</td>
    <td>&yen;15</td>
    <td><a href="https://akizukidenshi.com/catalog/g/g112255/">秋月電子</a></td>
  </tr>
  <tr>
    <td colspan="8" align="center">
      <ins>marutsu</ins>
    </td>
  </tr>
  <tr>
    <td>25</td>
    <td>コネクタハウジング<br>(2極、ピッチ：1.25mm、1列)</td>
    <td>¥41</td>
    <td>10</td>
    <td>¥410</td>
    <td><a href="https://www.marutsu.co.jp/pc/i/2566668/">marutsu</a></td>
    <td><u></u></td>
    <!-- no.24 と no.25 の備考を結合 -->
    <td rowspan="2">
      No. 25, 26 のどちらかが在庫切れの場合，<br>
      ▼リンク先の商品で代用可能です．<br>
      <a href="https://www.marutsu.co.jp/pc/i/2231331/">代替リンク</a>
    </td>
  </tr>
  <tr>
    <td>26</td>
    <td>1.25mmピッチターミナル【500588000】</td>
    <td>¥9</td>
    <td>4</td>
    <td>¥36</td>
    <td><a href="https://www.marutsu.co.jp/pc/i/584344/">marutsu</a></td>
    <td></td>
    <!-- 備考セルは結合しているため省略 -->
  </tr>
  <tr>
    <td>27</td>
    <td>BATT CHARGER OPEN FRAME 5V 2A<br>【DFR1026】</td>
    <td>&yen;662</td>
    <td>1</td>
    <td>&yen;662</td>
    <td><a href="https://www.marutsu.co.jp/pc/i/43483335/">marutsu</a></td>
    <td><a href="https://www.aitendo.com/product/20089">aitendo</a></td>
    <td></td>
  </tr>
  <tr>
    <td>28</td>
    <td>リチウムイオンポリマー電池<br>(3.7V、1200mAh)【DTP673450(PHR)】</td>
    <td>&yen;2,363</td>
    <td>1</td>
    <td>&yen;2,363</td>
    <td><a href="https://www.marutsu.co.jp/pc/i/1634091/">marutsu</a></td>
    <td></td>
    <td></td>
  </tr>
  <tr>
    <td>29</td>
    <td>ミニモーター低速ギヤボックス(4速)<br>【ITEM70189】</td>
    <td>&yen;946</td>
    <td>2</td>
    <td>&yen;1,892</td>
    <td><a href="https://www.marutsu.co.jp/pc/i/159903/">marutsu</a></td>
    <td><a href="https://amzn.to/3Kh5m9R">Amazon</a></td>
    <td></td>
  </tr>
  <tr>
    <td colspan="8" align="center">
      <ins>Amazon</ins>
    </td>
  </tr>
  <tr>
    <td>30</td>
    <td>3mm六角シャフトセット<br>【ITEM70252】</td>
    <td>&yen;280</td>
    <td>1</td>
    <td>&yen;280</td>
    <td><a href="https://amzn.to/3I9S5iY">Amazon</a></td>
    <td></td>
    <td>38 [mm] 2本を，ギヤボックス付属のシャフトの代わりに使用します．</td>
  </tr>
  <tr>
    <td>31</td>
    <td>PolyTerra PLA 1.75mm径 1000g<br>Sunrise Orange</td>
    <td>&yen;3,278</td>
    <td>1</td>
    <td>&yen;3,278</td>
    <td><a href="https://amzn.to/4gVXI1b">Amazon</a></td>
    <td></td>
    <td rowspan="2">
      約50 [g]ずつ使用<br>
      ▼調達困難な方向けに，印刷物の販売も実施中<br>
      <a href="https://korokoro-robot.booth.pm/items/6812764">https://korokoro-robot.booth.pm/items/6812764</a>
    </td>
  </tr>
  <tr>
    <td>32</td>
    <td>eSUN Flexible TPU 白</td>
    <td>&yen;3,999</td>
    <td>1</td>
    <td>&yen;3,999</td>
    <td><a href="https://amzn.to/46RzRvW">Amazon</a></td>
    <td></td>
    <!-- 備考セルは上の行と結合しているため省略 -->
  </tr>
  <tr>
    <td colspan="8" align="center">
      <ins>その他</ins>
    </td>
  </tr>
  <tr>
    <td>33</td>
    <td>ショートワイヤ付き<br>ミニ楕円形スピーカー（8Ω 1W）</td>
    <td>&yen;486</td>
    <td>1</td>
    <td>&yen;486</td>
    <td><a href="https://ssci.to/5804">SWITCH<br>SCIENCE</a></td>
    <td><a href="https://www.marutsu.co.jp/pc/i/32844060/">marutsu</a></td>
    <td></td>
  </tr>
  <tr>
    <td>34</td>
    <td>収縮チューブ SCG1.0-1B</td>
    <td>&yen;67</td>
    <td>1</td>
    <td>&yen;67</td>
    <td><a href="https://www.monotaro.com/p/1838/1238/?t.q=%94M%88%B3%8Fk">モノタロウ</a></td>
    <td></td>
    <td></td>
  </tr>
  <tr>
    <td>35</td>
    <td>UL1571耐熱架橋ビニル絶縁電線<br>UL1571 AWG30 2m &lt;6&gt;</td>
    <td>&yen;967</td>
    <td>1</td>
    <td>&yen;967</td>
    <td><a href="https://www.monotaro.com/p/4486/8400/?t.q=awg30">モノタロウ</a></td>
    <td></td>
    <td></td>
  </tr>
  <tr>
    <td>36</td>
    <td>100mm空カプセル　10個入り<br>（クリアタイプ）</td>
    <td>&yen;1,155</td>
    <td>1</td>
    <td>&yen;1,155</td>
    <td><a href="https://www.a-muzu.com/category/EMPTY_CAPSULE_008/C0531.html">あミューズ</a></td>
    <td></td>
    <td>1体あたり1個です．．．あと9体</td>
  </tr>
  <tr>
    <td>37</td>
    <td>〈第2.1世代〉ころボ<br>メインボード</td>
    <td>&yen;3,583</td>
    <td>1</td>
    <td>&yen;3,583</td>
    <td>JCBgogo</td>
    <td></td>
    <td>
      基板費用＋輸送費（DHL）から算出．最低5枚から．<br>
      ▼調達困難な方向けに，印刷物の販売も実施中<br>
      <a href="https://korokoro-robot.booth.pm/items/6807081">https://korokoro-robot.booth.pm/items/6807081</a>
    </td>
  </tr>
</table>
</details>

### 3Dプリンタ部品 / Model
<table>
  <tr>
    <th style="text-align:center;" rowspan="2">No.</th>
    <th style="text-align:center;" rowspan="2">品名</th>
    <th style="text-align:center;">単価</th>
    <th style="text-align:center;" rowspan="2">個数</th>
    <th style="text-align:center;">小計</th>
    <th style="text-align:center;" colspan="2">調達先</th>
    <th style="text-align:center;" rowspan="2">備考</th>
  </tr>
  <tr>
    <th style="text-align:center;">a</th>
    <th style="text-align:center;">a</th>
    <th style="text-align:center;">a</th>
    <th style="text-align:center;">b</th>
  </tr>
  <tr>
    <td colspan="8" align="center">
      <ins>3D プリンタ　お持ちの方</ins>
    </td>
  </tr>
  <tr>
    <td>M1_1</td>
    <td>PolyTerra PLA 1.75mm径 1000g<br>Sunrise Orange</td>
    <td>&yen;3,278</td>
    <td>1</td>
    <td>&yen;3,278</td>
    <td><a href="https://amzn.to/4gVXI1b">Amazon</a></td>
    <td></td>
    <td rowspan="2">
      約50 [g]ずつ使用
    </td>
  </tr>
  <tr>
    <td>M2_1</td>
    <td>eSUN Flexible TPU 白</td>
    <td>&yen;3,999</td>
    <td>1</td>
    <td>&yen;3,999</td>
    <td><a href="https://amzn.to/46RzRvW">Amazon</a></td>
    <td></td>
    <!-- 備考セルは上の行と結合しているため省略 -->
  </tr>
  <tr>
    <td colspan="8" align="center">
      <ins>3D プリンタ　お持ちでない方</ins>
    </td>
  </tr>
  <tr>
    <td>M1_2</td>
    <td>組み立てサポート品<br>〈第2.1世代〉ころボ　3Dプリンタ製パーツ</td>
    <td>&yen;2,350</td>
    <td>1</td>
    <td>&yen;2,350</td>
    <td><a href="https://korokoro-robot.booth.pm/items/6812764">BOOTH</a></td>
    <td></td>
    <td>送料別</td>
  </tr>
</table>

### 駆動ユニット / Actuator
<table>
  <tr>
    <th style="text-align:center;" rowspan="2">No.</th>
    <th style="text-align:center;" rowspan="2">品名</th>
    <th style="text-align:center;">単価</th>
    <th style="text-align:center;" rowspan="2">個数</th>
    <th style="text-align:center;">小計</th>
    <th style="text-align:center;" colspan="2">調達先</th>
    <th style="text-align:center;" rowspan="2">備考</th>
  </tr>
  <tr>
    <th style="text-align:center;">a</th>
    <th style="text-align:center;">a</th>
    <th style="text-align:center;">a</th>
    <th style="text-align:center;">b</th>
  </tr>
  <tr>
    <td>A1</td>
    <td>ミニモーター低速ギヤボックス(4速)<br>【ITEM70189】</td>
    <td>&yen;946</td>
    <td>2</td>
    <td>&yen;1,892</td>
    <td><a href="https://www.marutsu.co.jp/pc/i/159903/">marutsu</a></td>
    <td><a href="https://amzn.to/3Kh5m9R">Amazon</a></td>
    <td></td>
  </tr>
  <tr>
    <td>A2</td>
    <td>3mm六角シャフトセット<br>【ITEM70252】</td>
    <td>&yen;280</td>
    <td>1</td>
    <td>&yen;280</td>
    <td><a href="https://amzn.to/3I9S5iY">Amazon</a></td>
    <td></td>
    <td>38 [mm] 2本を，ギヤボックス付属のシャフトの代わりに使用します．</td>
  </tr>
</table>

### メインボード / Board
<table>
  <tr>
    <th style="text-align:center;" rowspan="2">No.</th>
    <th style="text-align:center;" rowspan="2">品名</th>
    <th style="text-align:center;">単価</th>
    <th style="text-align:center;" rowspan="2">個数</th>
    <th style="text-align:center;">小計</th>
    <th style="text-align:center;" colspan="2">調達先</th>
    <th style="text-align:center;" rowspan="2">備考</th>
  </tr>
  <tr>
    <th style="text-align:center;">a</th>
    <th style="text-align:center;">a</th>
    <th style="text-align:center;">a</th>
    <th style="text-align:center;">b</th>
  </tr>
  <tr>
    <td colspan="8" align="center">
      <ins>基板業者へ発注される方</ins>
    </td>
  </tr>
  <tr>
    <td>B1_1</td>
    <td>〈第2.1世代〉ころボ<br>メインボード（基板）</td>
    <td>&yen;3,583</td>
    <td>1</td>
    <td>&yen;3,583</td>
    <td>JCBgogo</td>
    <td></td>
    <td>
      基板費用＋輸送費（DHL）から算出．最低5枚から．<br>
    </td>
  </tr>
  <tr>
    <td colspan="8" align="center">
      <ins>基板完成品を調達される方</ins>
    </td>
  </tr>
  <tr>
    <td>B1_2</td>
    <td>組み立てサポート品<br>〈第2.1世代〉ころボ<br>メインボード（基板）</td>
    <td>&yen;1,000</td>
    <td>1</td>
    <td>&yen;1,000</td>
    <td><a href="https://korokoro-robot.booth.pm/items/6807081">BOOTH</a></td>
    <td></td>
    <td>送料別</td>
  </tr>
  <tr>
    <td colspan="8" align="center">
      <ins>共通</ins>
    </td>
  </tr>
  <tr>
    <td>B2</td>
    <td>Raspberry Pi Pico</td>
    <td>¥770</td>
    <td>1</td>
    <td>¥770</td>
    <td><a href="https://akizukidenshi.com/catalog/g/g116132/">秋月電子</a></td>
    <td><a href="https://ssci.to/6900">SWITCH<br>SCIENCE</a></td>
    <td></td>
  </tr>
  <tr>
    <td>B3</td>
    <td>BNO055使用 9軸センサー<br>フュージョンモジュールキット</td>
    <td>¥2,450</td>
    <td>1</td>
    <td>¥2,450</td>
    <td><a href="https://akizukidenshi.com/catalog/g/g116996/">秋月電子</a></td>
    <td></td>
    <td></td>
  </tr>
  <tr>
    <td>B4</td>
    <td>SPV1840LR5H-B使用<br>シリコンマイクモジュールキット</td>
    <td>¥450</td>
    <td>1</td>
    <td>¥450</td>
    <td><a href="https://akizukidenshi.com/catalog/g/g116573/">秋月電子</a></td>
    <td></td>
    <td></td>
  </tr>
  <tr>
    <td>B5</td>
    <td>TC78H653FTG<br>モータードライバーモジュール</td>
    <td>¥200</td>
    <td>1</td>
    <td>¥200</td>
    <td><a href="https://akizukidenshi.com/catalog/g/g114746/">秋月電子</a></td>
    <td></td>
    <td></td>
  </tr>
  <tr>
    <td>B6</td>
    <td>音声合成LSI ATP3011F1-PU<br>(ゆっくりな女性の音声)</td>
    <td>¥1,050</td>
    <td>1</td>
    <td>¥1,050</td>
    <td><a href="https://akizukidenshi.com/catalog/g/g106220/">秋月電子</a></td>
    <td></td>
    <td></td>
  </tr>
  <tr>
    <td>B7</td>
    <td>PAM8012使用2ワット<br>D級アンプモジュール</td>
    <td>¥300</td>
    <td>1</td>
    <td>¥300</td>
    <td><a href="https://akizukidenshi.com/catalog/g/g108217/">秋月電子</a></td>
    <td></td>
    <td></td>
  </tr>
  <tr>
    <td>B8</td>
    <td>カーボン抵抗 1/2W150kΩ</td>
    <td>¥100</td>
    <td>1</td>
    <td>¥100</td>
    <td><a href="https://akizukidenshi.com/catalog/g/g107855/">秋月電子</a></td>
    <td></td>
    <td></td>
  </tr>
  <tr>
    <td>B9</td>
    <td>積層セラミックコンデンサー<br>0.1μF50V X7R 2.54mm 10個</td>
    <td>¥100</td>
    <td>1</td>
    <td>¥100</td>
    <td><a href="https://akizukidenshi.com/catalog/g/g113582/">秋月電子</a></td>
    <td></td>
    <td></td>
  </tr>
  <tr>
    <td>B10</td>
    <td>電解コンデンサー100μ<br>F25V105℃ ルビコンPX</td>
    <td>¥10</td>
    <td>1</td>
    <td>¥10</td>
    <td><a href="https://akizukidenshi.com/catalog/g/g117877/">秋月電子</a></td>
    <td></td>
    <td></td>
  </tr>
  <tr>
    <td>B11</td>
    <td>分割ロングピンソケット 1×42 (42P)</td>
    <td>¥80</td>
    <td>3</td>
    <td>¥240</td>
    <td><a href="https://akizukidenshi.com/catalog/g/g105779/">秋月電子</a></td>
    <td></td>
    <td></td>
  </tr>
  <tr>
    <td>B12</td>
    <td>ピンヘッダー 1×40 (40P)</td>
    <td>¥35</td>
    <td>3</td>
    <td>¥105</td>
    <td><a href="https://akizukidenshi.com/catalog/g/g100167/">秋月電子</a></td>
    <td></td>
    <td></td>
  </tr>
  <tr>
    <td>B13</td>
    <td>ピンソケット 1×20 (20P)<br>リード長10mm</td>
    <td>¥60</td>
    <td>2</td>
    <td>¥120</td>
    <td><a href="https://akizukidenshi.com/catalog/g/g118376/">秋月電子</a></td>
    <td><a href="https://ssci.to/8027">SWITCH<br>SCIENCE</a></td>
    <td></td>
  </tr>
  <tr>
    <td>B14</td>
    <td>ICソケット (28P) スリム300milタイプ</td>
    <td>&yen;280</td>
    <td>1</td>
    <td>&yen;280</td>
    <td><a href="https://akizukidenshi.com/catalog/g/g100013/">秋月電子</a></td>
    <td></td>
    <td></td>
  </tr>
  <tr>
    <td>B15</td>
    <td>BATT CHARGER OPEN FRAME 5V 2A【DFR1026】</td>
    <td>&yen;662</td>
    <td>1</td>
    <td>&yen;662</td>
    <td><a href="https://www.marutsu.co.jp/pc/i/43483335/">marutsu</a></td>
    <td><a href="https://www.aitendo.com/product/20089">aitendo</a></td>
    <td></td>
  </tr>
</table>

### 配線 / Wire
<table>
  <tr>
    <th style="text-align:center;" rowspan="2">No.</th>
    <th style="text-align:center;" rowspan="2">品名</th>
    <th style="text-align:center;">単価</th>
    <th style="text-align:center;" rowspan="2">個数</th>
    <th style="text-align:center;">小計</th>
    <th style="text-align:center;" colspan="2">調達先</th>
    <th style="text-align:center;" rowspan="2">備考</th>
  </tr>
  <tr>
    <th style="text-align:center;">a</th>
    <th style="text-align:center;">a</th>
    <th style="text-align:center;">a</th>
    <th style="text-align:center;">b</th>
  </tr>
  <tr>
    <td>W1</td>
    <td>コネクター用ハウジング 2P</td>
    <td>¥10</td>
    <td>1</td>
    <td>¥10</td>
    <td><a href="https://akizukidenshi.com/catalog/g/g112151">秋月電子</a></td>
    <td></td>
    <td></td>
  </tr>
  <tr>
    <td>W2</td>
    <td>コネクター用ハウジング 4P</td>
    <td>&yen;10</td>
    <td>1</td>
    <td>&yen;10</td>
    <td><a href="https://akizukidenshi.com/catalog/g/g112153/">秋月電子</a></td>
    <td><u></u></td>
    <td rowspan="2">
      ピンソケットでも対応できます．<br>
      ▼コネクター側だけ利用する手法もあります．<br>
      <a href="https://eleshop.jp/shop/g/gAAC41C/?srsltid=AfmBOoqFBb0585i-U3NJiWO_EpqYxHgdgGQ-2iUeOSxdOJOnOQ2duirH0ts">共立エレショップ</a>
    </td>
  </tr>
  <tr>
    <td>W3</td>
    <td>ケーブル用コネクター 10個</td>
    <td>&yen;50</td>
    <td>1</td>
    <td>&yen;50</td>
    <td><a href="https://akizukidenshi.com/catalog/g/g112160">秋月電子</a></td>
    <td><u></u></td>
    <!-- 備考セルは上の行と結合しているため省略 -->
  </tr>
  <tr>
    <td>W4</td>
    <td>PHコネクター ベース付ポスト<br>トップ型 2P B2B-PH-K-S</td>
    <td>&yen;10</td>
    <td>1</td>
    <td>&yen;10</td>
    <td><a href="https://akizukidenshi.com/catalog/g/g112802/">秋月電子</a></td>
    <td><a href="https://amzn.to/4nIFLoP">Amazon</a></td>
    <td rowspan="6">候補2のAmazonから調達したほうが，部品を紛失してもある程度予備を確保しつつ，専用ケースで保管できるため，扱いやすいかもです．</td>
  </tr>
  <tr>
    <td>W5</td>
    <td>XHコネクター ベース付ポスト<br>トップ型 2P B2B-XH-A(LF)(SN)</td>
    <td>&yen;10</td>
    <td>3</td>
    <td>&yen;30</td>
    <td><a href="https://akizukidenshi.com/catalog/g/g112247/">秋月電子</a></td>
    <td rowspan="5"><a href="https://amzn.to/42ELjbL">Amazon</a></td>
  </tr>
  <tr>
    <td>W6</td>
    <td>XHコネクター ベース付ポスト<br>トップ型 4P B4B-XH-A(LF)(SN)</td>
    <td>&yen;10</td>
    <td>1</td>
    <td>&yen;10</td>
    <td><a href="https://akizukidenshi.com/catalog/g/g112249/">秋月電子</a></td>
  </tr>
  <tr>
    <td>W7</td>
    <td>XHコネクター ハウジング用コンタクト<br>SXH-001T-P0.6</td>
    <td>&yen;200</td>
    <td>1</td>
    <td>&yen;200</td>
    <td><a href="https://akizukidenshi.com/catalog/g/g112265/">秋月電子</a></td>
  </tr>
  <tr>
    <td>W8</td>
    <td>XHコネクター ハウジング 4P XHP-4</td>
    <td>&yen;5</td>
    <td>1</td>
    <td>&yen;5</td>
    <td><a href="https://akizukidenshi.com/catalog/g/g112257/">秋月電子</a></td>
  </tr>
  <tr>
    <td>W9</td>
    <td>XHコネクター ハウジング 2P XHP-2</td>
    <td>&yen;5</td>
    <td>3</td>
    <td>&yen;15</td>
    <td><a href="https://akizukidenshi.com/catalog/g/g112255/">秋月電子</a></td>
  </tr>
  <tr>
    <td>W10</td>
    <td>コネクタハウジング<br>(2極、ピッチ：1.25mm、1列)</td>
    <td>¥41</td>
    <td>10</td>
    <td>¥410</td>
    <td><a href="https://www.marutsu.co.jp/pc/i/2566668/">marutsu</a></td>
    <td><u></u></td>
    <!-- no.24 と no.25 の備考を結合 -->
    <td rowspan="2">
      No. W10, W11 のどちらかが在庫切れの場合，<br>
      ▼リンク先の商品で代用可能です．<br>
      <a href="https://www.marutsu.co.jp/pc/i/2231331/">代替リンク</a>
    </td>
  </tr>
  <tr>
    <td>W11</td>
    <td>1.25mmピッチターミナル【500588000】</td>
    <td>¥9</td>
    <td>4</td>
    <td>¥36</td>
    <td><a href="https://www.marutsu.co.jp/pc/i/584344/">marutsu</a></td>
    <td></td>
    <!-- 備考セルは結合しているため省略 -->
  </tr>
</table>

### その他 / Other
<table>
  <tr>
    <th style="text-align:center;" rowspan="2">No.</th>
    <th style="text-align:center;" rowspan="2">品名</th>
    <th style="text-align:center;">単価</th>
    <th style="text-align:center;" rowspan="2">個数</th>
    <th style="text-align:center;">小計</th>
    <th style="text-align:center;" colspan="2">調達先</th>
    <th style="text-align:center;" rowspan="2">備考</th>
  </tr>
  <tr>
    <th style="text-align:center;">a</th>
    <th style="text-align:center;">a</th>
    <th style="text-align:center;">a</th>
    <th style="text-align:center;">b</th>
  </tr>
  <tr>
    <td>O1</td>
    <td>0.96インチ 128×64ドット<br>有機ELディスプレイ(OLED) 白色</td>
    <td>¥580</td>
    <td>1</td>
    <td>¥580</td>
    <td><a href="https://akizukidenshi.com/catalog/g/g112031/">秋月電子</a></td>
    <td></td>
    <td></td>
  </tr>
  <tr>
    <td>O2</td>
    <td>照度センサー<br>NJL7302L-F3</td>
    <td>¥45</td>
    <td>1</td>
    <td>¥45</td>
    <td><a href="https://akizukidenshi.com/catalog/g/g108910/">秋月電子</a></td>
    <td></td>
    <td></td>
  </tr>
  <tr>
    <td>O3</td>
    <td>ショートワイヤ付き<br>ミニ楕円形スピーカー（8Ω 1W）</td>
    <td>&yen;486</td>
    <td>1</td>
    <td>&yen;486</td>
    <td><a href="https://ssci.to/5804">SWITCH<br>SCIENCE</a></td>
    <td><a href="https://www.marutsu.co.jp/pc/i/32844060/">marutsu</a></td>
    <td></td>
  </tr>
  <tr>
    <td>O4</td>
    <td>リチウムイオンポリマー電池<br>(3.7V、1200mAh)【DTP673450(PHR)】</td>
    <td>&yen;2,363</td>
    <td>1</td>
    <td>&yen;2,363</td>
    <td><a href="https://www.marutsu.co.jp/pc/i/1634091/">marutsu</a></td>
    <td></td>
    <td></td>
  </tr>
  <tr>
    <td>O5</td>
    <td>収縮チューブ SCG1.0-1B</td>
    <td>&yen;67</td>
    <td>1</td>
    <td>&yen;67</td>
    <td><a href="https://www.monotaro.com/p/1838/1238/?t.q=%94M%88%B3%8Fk">モノタロウ</a></td>
    <td></td>
    <td></td>
  </tr>
  <tr>
    <td>O6</td>
    <td>UL1571耐熱架橋ビニル絶縁電線<br>UL1571 AWG30 2m &lt;6&gt;</td>
    <td>&yen;967</td>
    <td>1</td>
    <td>&yen;967</td>
    <td><a href="https://www.monotaro.com/p/4486/8400/?t.q=awg30">モノタロウ</a></td>
    <td></td>
    <td></td>
  </tr>
  <tr>
    <td>O7</td>
    <td>100mm空カプセル　10個入り<br>（クリアタイプ）</td>
    <td>&yen;1,155</td>
    <td>1</td>
    <td>&yen;1,155</td>
    <td><a href="https://www.a-muzu.com/category/EMPTY_CAPSULE_008/C0531.html">あミューズ</a></td>
    <td></td>
    <td>1体あたり1個です．．．あと9体</td>
  </tr>
</table>

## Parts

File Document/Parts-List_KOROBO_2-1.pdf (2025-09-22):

No. | 品名 | 単価 | 個数 | 小計 ※候補1 | 購入先 購入先 （候補1） （候補2） | 備考
1 | Raspberry Pi Pico | ¥770 | 1 | ¥770 | 秋月電子 SWITCH SCIENCE
2 | 0.96インチ 128×64ドット 有機ELディスプレイ(OLED) 白色 | ¥580 | 1 | ¥580 | 秋月電子
3 | BNO055使用 9軸センサー フュージョンモジュールキット | ¥2,450 | 1 | ¥2,450 | 秋月電子
4 | SPV1840LR5H-B使用 シリコンマイクモジュールキット | ¥450 | 1 | ¥450 | 秋月電子
5 | TC78H653FTG モータードライバーモジュール | ¥200 | 1 | ¥200 | 秋月電子
6 | 音声合成LSI ATP3011F1-PU (ゆっくりな女性の音声) | ¥1,050 | 1 | ¥1,050 | 秋月電子
7 | PAM8012使用2ワット D級アンプモジュール | ¥300 | 1 | ¥300 | 秋月電子
8 | 照度センサー NJL7302L-F3 | ¥45 | 1 | ¥45 | 秋月電子
9 | カーボン抵抗 1/2W150kΩ | ¥100 | 1 | ¥100 | 秋月電子
10 | 積層セラミックコンデンサー 0.1μF50V X7R 2.54mm 10個 | ¥100 | 1 | ¥100 | 秋月電子
11 | 電解コンデンサー100μ F25V105℃ ルビコンPX | ¥10 | 1 | ¥10 | 秋月電子
12 | 分割ロングピンソケット 1×42 (42P) | ¥80 | 3 | ¥240 | 秋月電子
13 | ピンヘッダー 1×40 (40P) | ¥35 | 3 | ¥105 | 秋月電子
14 | ピンソケット 1×20 (20P) リード⾧10mm | ¥60 | 2 | ¥120 | 秋月電子 SWITCH SCIENCE
15 | コネクター用ハウジング 2P | ¥10 | 1 | ¥10 | 秋月電子
16 | コネクター用ハウジング 4P | ¥10 | 1 | ¥10 | 秋月電子 | ピンソケットでも対応できます． ▼コネクター側だけ利用する手法もあります． 共立エレショップ
17 | ケーブル用コネクター 10個 | ¥50 | 1 | ¥50 | 秋月電子
18 | ICソケット (28P) スリム300milタイプ | ¥280 | 1 | ¥280 | 秋月電子
19 | PHコネクター ベース付ポスト トップ型 2P B2B-PH-K-S | ¥10 | 1 | ¥10 | 秋月電子 Amazon | 候補2のAmazonから購入したほうが，部品を紛失し てもある程度予備を確保しつつ，専用ケースで保管で きるため，扱いやすいかもです．
20 21 22 23 24 | XHコネクター ベース付ポスト トップ型 2P B2B-XH-A(LF)(SN) XHコネクター ベース付ポスト トップ型 4P B4B-XH-A(LF)(SN) XHコネクター ハウジング用コンタクト SXH-001T-P0.6 XHコネクター ハウジング 4P XHP-4 XHコネクター ハウジング 2P XHP-2 | ¥10 ¥10 ¥200 ¥5 ¥5 | 3 1 1 1 3 | ¥30 ¥10 ¥200 ¥5 ¥15 | 秋月電子 秋月電子 Amazon 秋月電子 秋月電子 秋月電子
25 | コネクタハウジング (2極、ピッチ：1.25mm、1列) | ¥41 | 10 | ¥410 | marutsu | No. 25, 26のどちらかが在庫切れの場合， ▼リンク先の商品で代用可能です． https://www.marutsu.co.jp/pc/i/2231331/
26 | 1.25mmピッチターミナル【500588000】 | ¥9 | 4 | ¥36 | marutsu
27 | BATT CHARGER OPEN FRAME 5V 2A 【DFR1026】 | ¥662 | 1 | ¥662 | marutsu aitendo
28 | リチウムイオンポリマー電池 (3.7V、1200mAh)【DTP673450(PHR)】 | ¥2,363 | 1 | ¥2,363 | marutsu
29 | ミニモーター低速ギヤボックス(4速) 【ITEM70189】 | ¥946 | 2 | ¥1,892 | marutsu Amazon
30 | 3mm六角シャフトセット | ¥280 | 1 | ¥280 | Amazon | 38 [mm] 2本を，ギヤボックス付属のシャフトの代わ りに使用します．
31 | ショートワイヤ付き ミニ楕円形スピーカー（8Ω 1W） | ¥486 | 1 | ¥486 | SWITCH marutsu SCIENCE
32 | 収縮チューブ SCG1.0-1B | ¥67 | 1 | ¥67 | モノタロウ
33 | UL1571耐熱架橋ビニル絶縁電線 UL1571 AWG30 2m <6> | ¥967 | 1 | ¥967 | モノタロウ
34 | 100mm空カプセル 10個入り （クリアタイプ） | ¥1,155 | 1 | ¥1,155 | あミューズ | 1体あたり1個です．．．あと9体
35 | 〈第2.1世代〉ころボ メインボード | ¥3,583 | 1 | ¥3,583 | JCBgogo | 基板費用＋輸送費（DHL）から算出．最低5枚から ▼調達困難な方向けに，印刷物の販売も実施中 https://korokoro-robot.booth.pm/items/6807081
36 | PolyTerra PLA 1.75mm径 1000g Sunrise Orange | ¥3,278 | 1 | ¥3,278 | Amazon | 約50 [g]ずつ使用 ▼調達困難な方向けに，印刷物の販売も実施中 https://korokoro-robot.booth.pm/items/6812764
37 | eSUN Flexible TPU 白 | ¥3,999 | 1 | ¥3,999 | Amazon

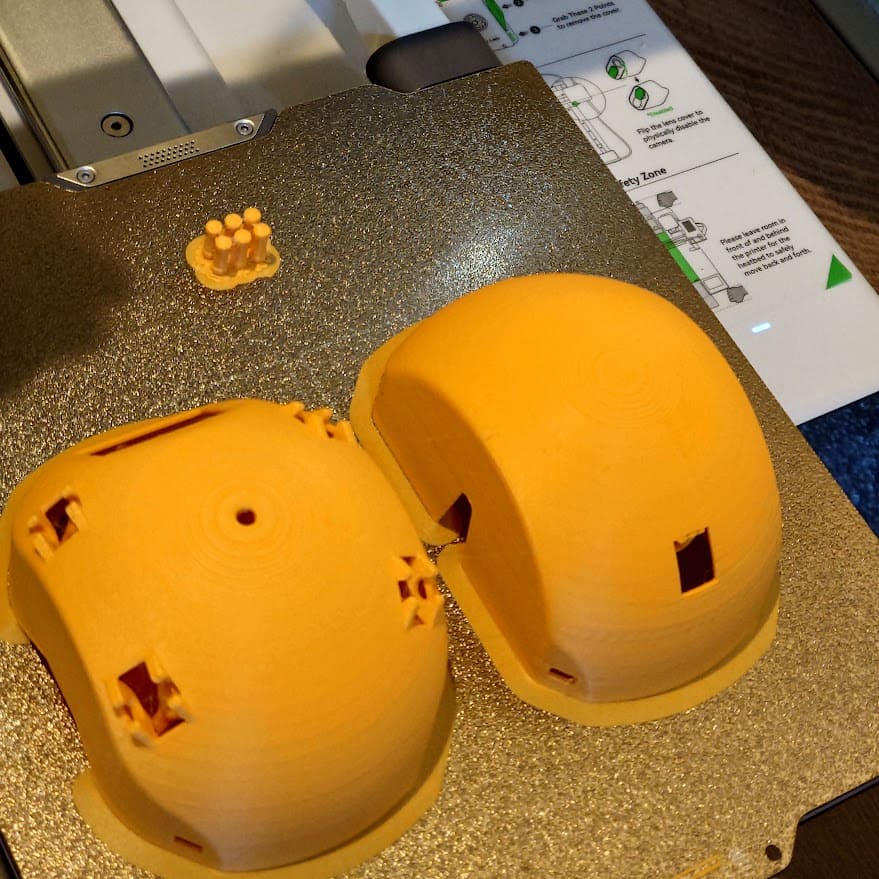
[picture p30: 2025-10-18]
Document/Picture/pla-parts_1.jpg

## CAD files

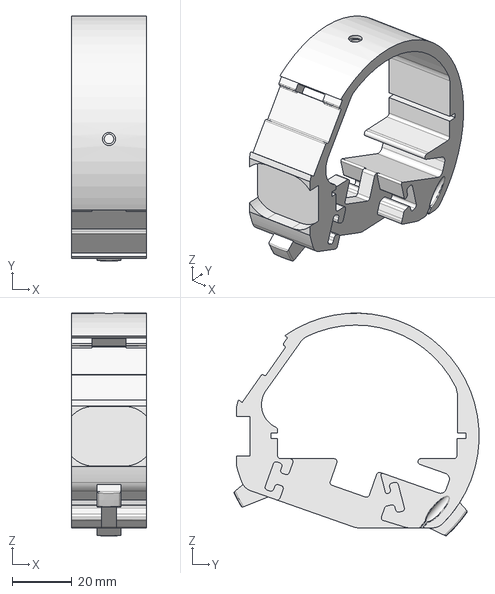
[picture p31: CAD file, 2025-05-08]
Model/STEP/main_frame_2-1.step
25.0 x 81.9 x 74.5 mm

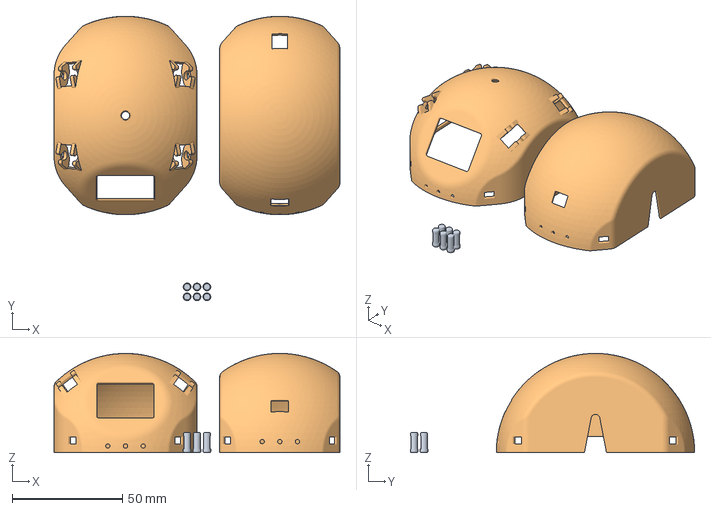
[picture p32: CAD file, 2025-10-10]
Model/korobo_2-1_PLA.3mf
129.7 x 129.0 x 45.0 mm
アセンブリ x 2

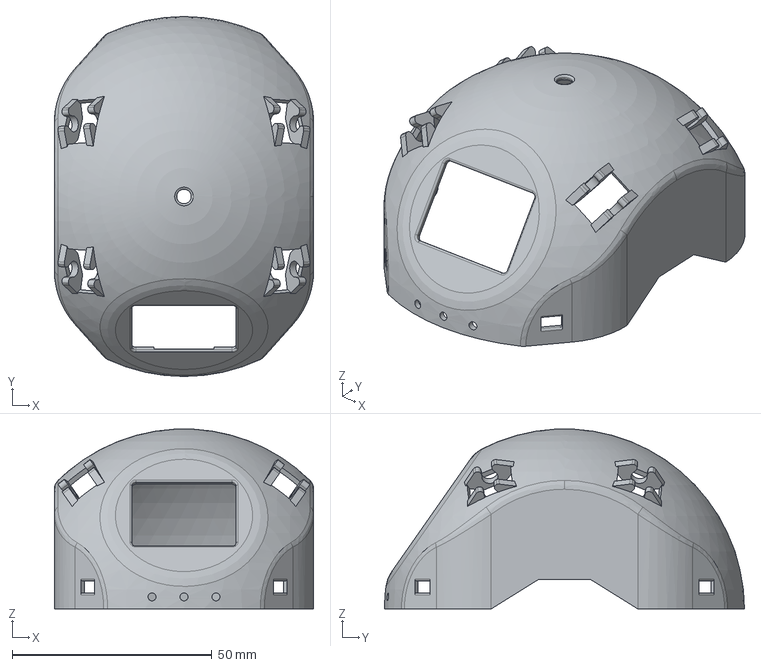
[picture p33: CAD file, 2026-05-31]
Model/STEP/cover_t_2-1.step
64.9 x 90.0 x 45.0 mm

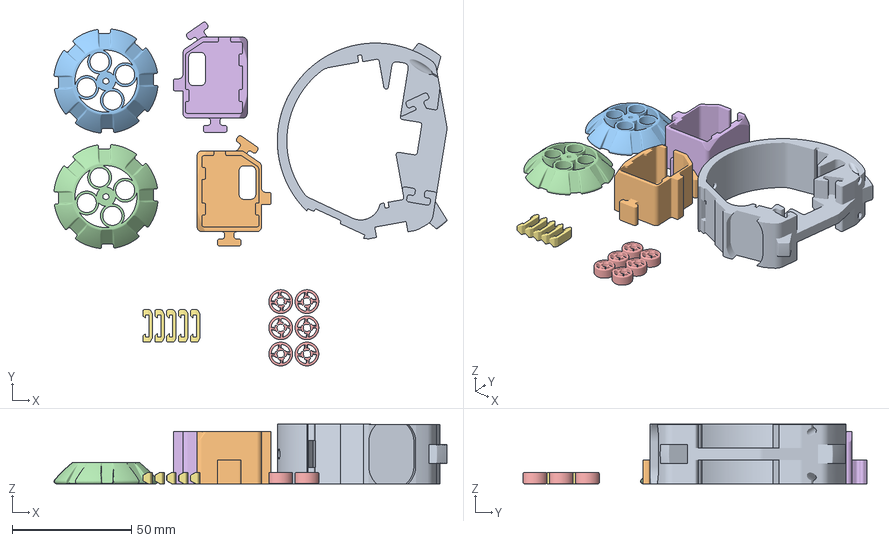
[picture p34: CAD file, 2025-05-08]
Model/korobo_2-1_TPU.3mf
165.0 x 144.3 x 25.0 mm
main_frame_2-1.step
motor_frame_2-1.step x 2
wheel_b_2-1.step x 2
アセンブリ x 2

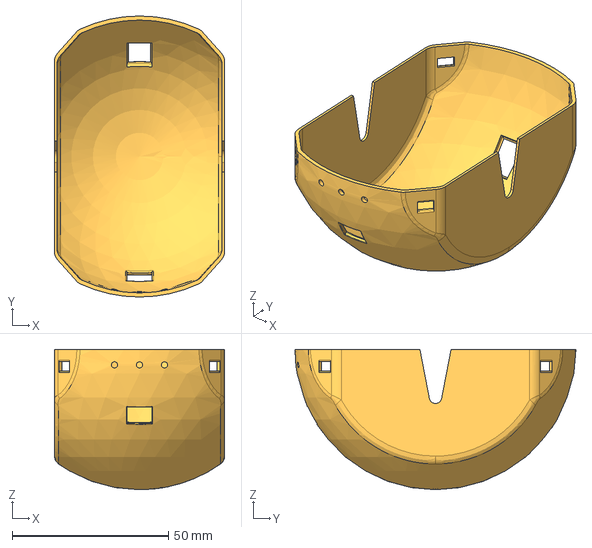
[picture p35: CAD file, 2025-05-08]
Model/STEP/cover_b_2-1.step
54.6 x 90.0 x 45.0 mm

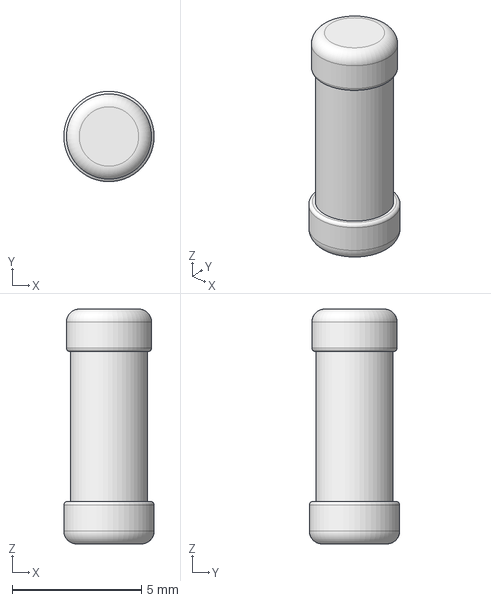
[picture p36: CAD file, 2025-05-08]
Model/STEP/wheel_t_shaft.step
3.50 x 3.50 x 9.10 mm

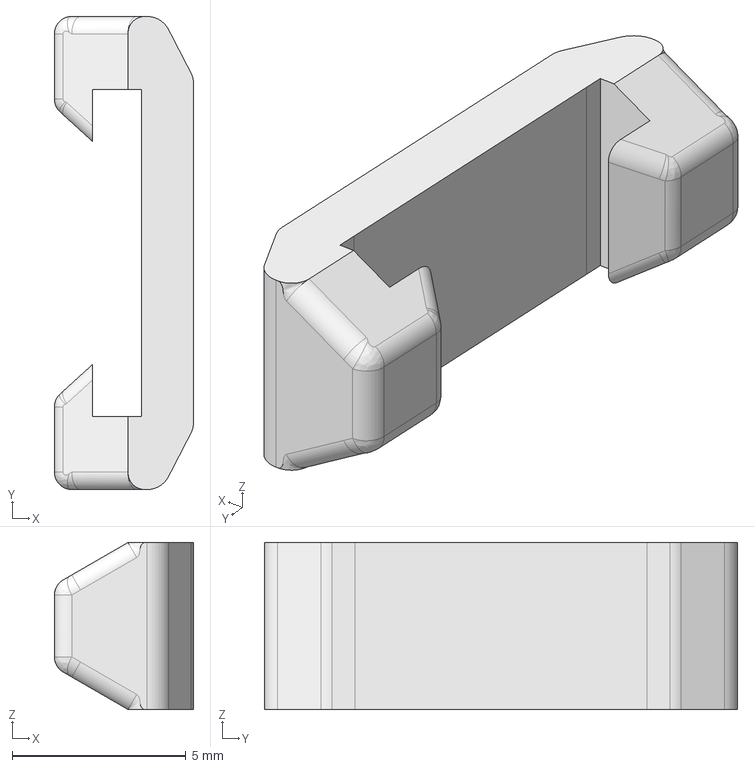
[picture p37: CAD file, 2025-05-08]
Model/STEP/cover_stopper.step
4.00 x 13.6 x 4.80 mm

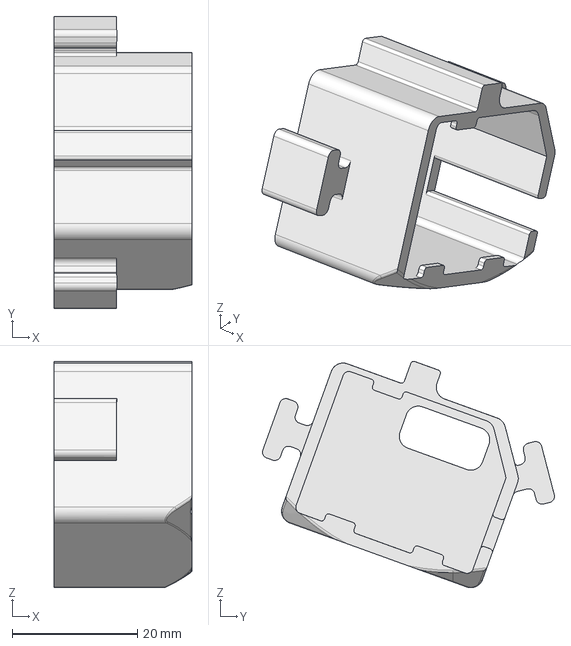
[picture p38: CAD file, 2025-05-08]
Model/STEP/motor_frame_2-1.step
22.0 x 46.6 x 36.1 mm

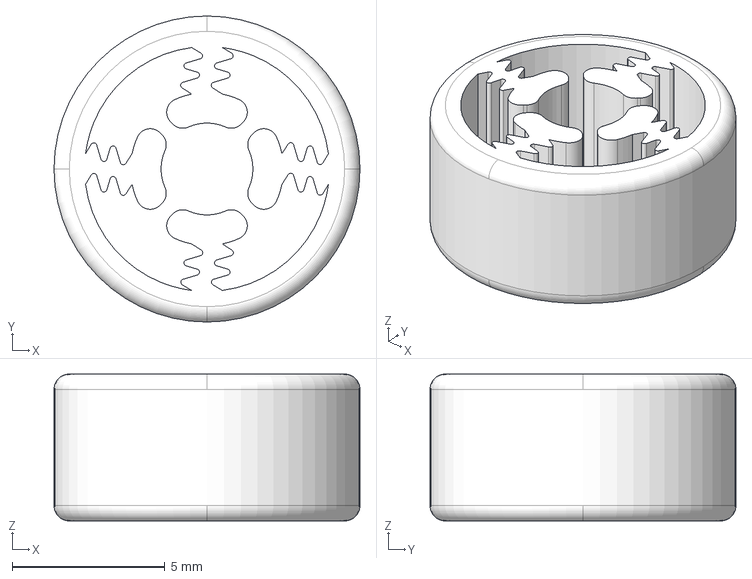
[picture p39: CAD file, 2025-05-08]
Model/STEP/wheel_t.step
10.0 x 10.0 x 4.80 mm

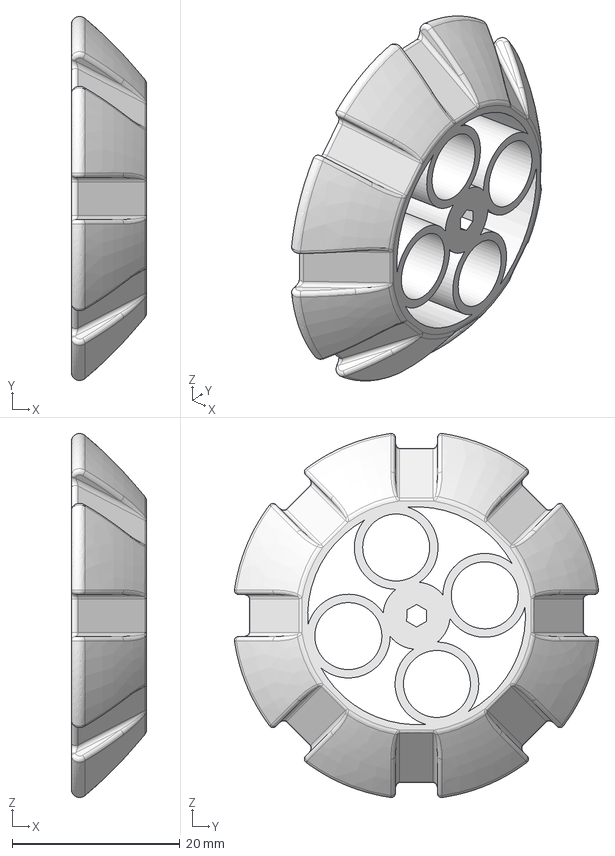
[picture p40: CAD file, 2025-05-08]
Model/STEP/wheel_b_2-1.step
9.00 x 43.5 x 43.5 mm

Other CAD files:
Model/STL(OLD)/main_frame_2-1.stl
Model/STL(OLD)/wheel_t_shaft.stl
Model/STL(OLD)/wheel_t.stl
Model/STL(OLD)/cover_stopper.stl
Model/STL(OLD)/wheel_b_2-1.stl
Model/STL(OLD)/motor_frame_2-1.stl
Model/STL(OLD)/cover_t_2-1.stl
Model/STL(OLD)/cover_b_2-1.stl
Model/STL/cover_b_2-1.stl
Model/STL/cover_stopper.stl
Model/STL/cover_t_2-1.stl
Model/STL/main_frame_2-1.stl
Model/STL/motor_frame_2-1.stl
Model/STL/wheel_b_2-1.stl
Model/STL/wheel_t.stl
Model/STL/wheel_t_shaft.stl

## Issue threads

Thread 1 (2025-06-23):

Reduce Physical Stress on OLED-Module Components

SoutaAtJp, 2025-06-23:
# OLEDモジュールの負荷軽減

OLEDディスプレイのモジュールにおいて，ディスプレイとモジュール基板間を接続するケーブル回りが損傷する事例を確認しました．
半年以上経ってからの発生でかつ，2体のうち1体のみに起きた事例なため，脅威度は高くありません．
しかし，長期的な活動に支障がでる可能性があり，今後対処する予定です．

## 対処法

### 外装モデルの修正
> ディスプレイとモジュール基板間をつなぐケーブル周囲にスペースをつくる．

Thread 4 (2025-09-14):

Enhancing Maximum Volume

SoutaAtJp, 2025-09-14:
# 最大音量の向上

現在，内部フレームの都合上，搭載スピーカーの性能を最大限引き出せていない．
そのため，カプセル内に ころボ がいると，声がほとんど聞こえない問題がある．

## 対処法

### 内部フレームモデルの修正
> スピーカー部品の後部接地面（内部フレーム）を一部くりぬき，ころボ の身体全体で音を振動させるような構造へ変更．

### スピーカー部品の再選定
> 可能性は低いが，より ころボ と相性が良いものを調査し，検証．

### アンプ部品の再選定

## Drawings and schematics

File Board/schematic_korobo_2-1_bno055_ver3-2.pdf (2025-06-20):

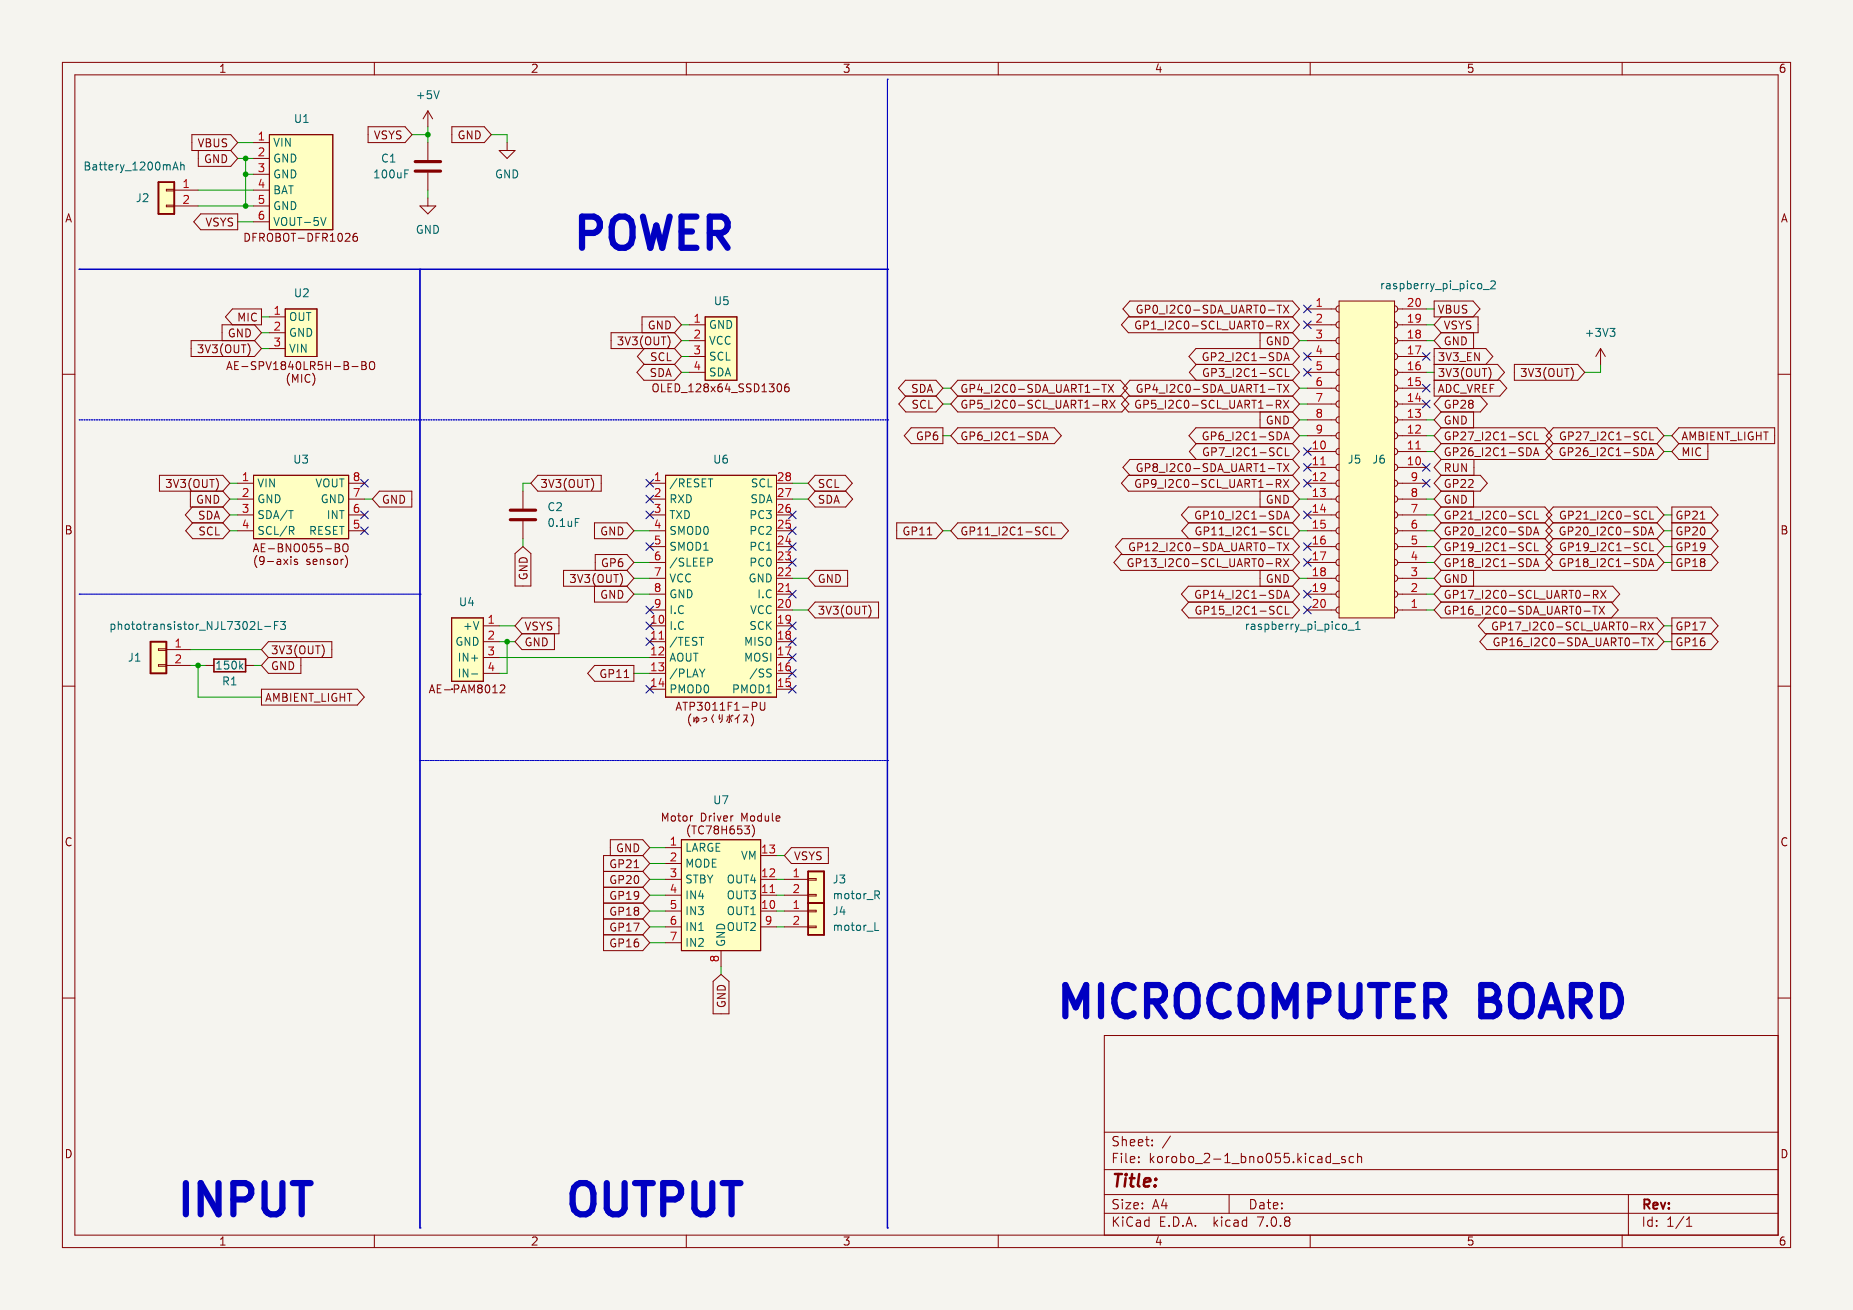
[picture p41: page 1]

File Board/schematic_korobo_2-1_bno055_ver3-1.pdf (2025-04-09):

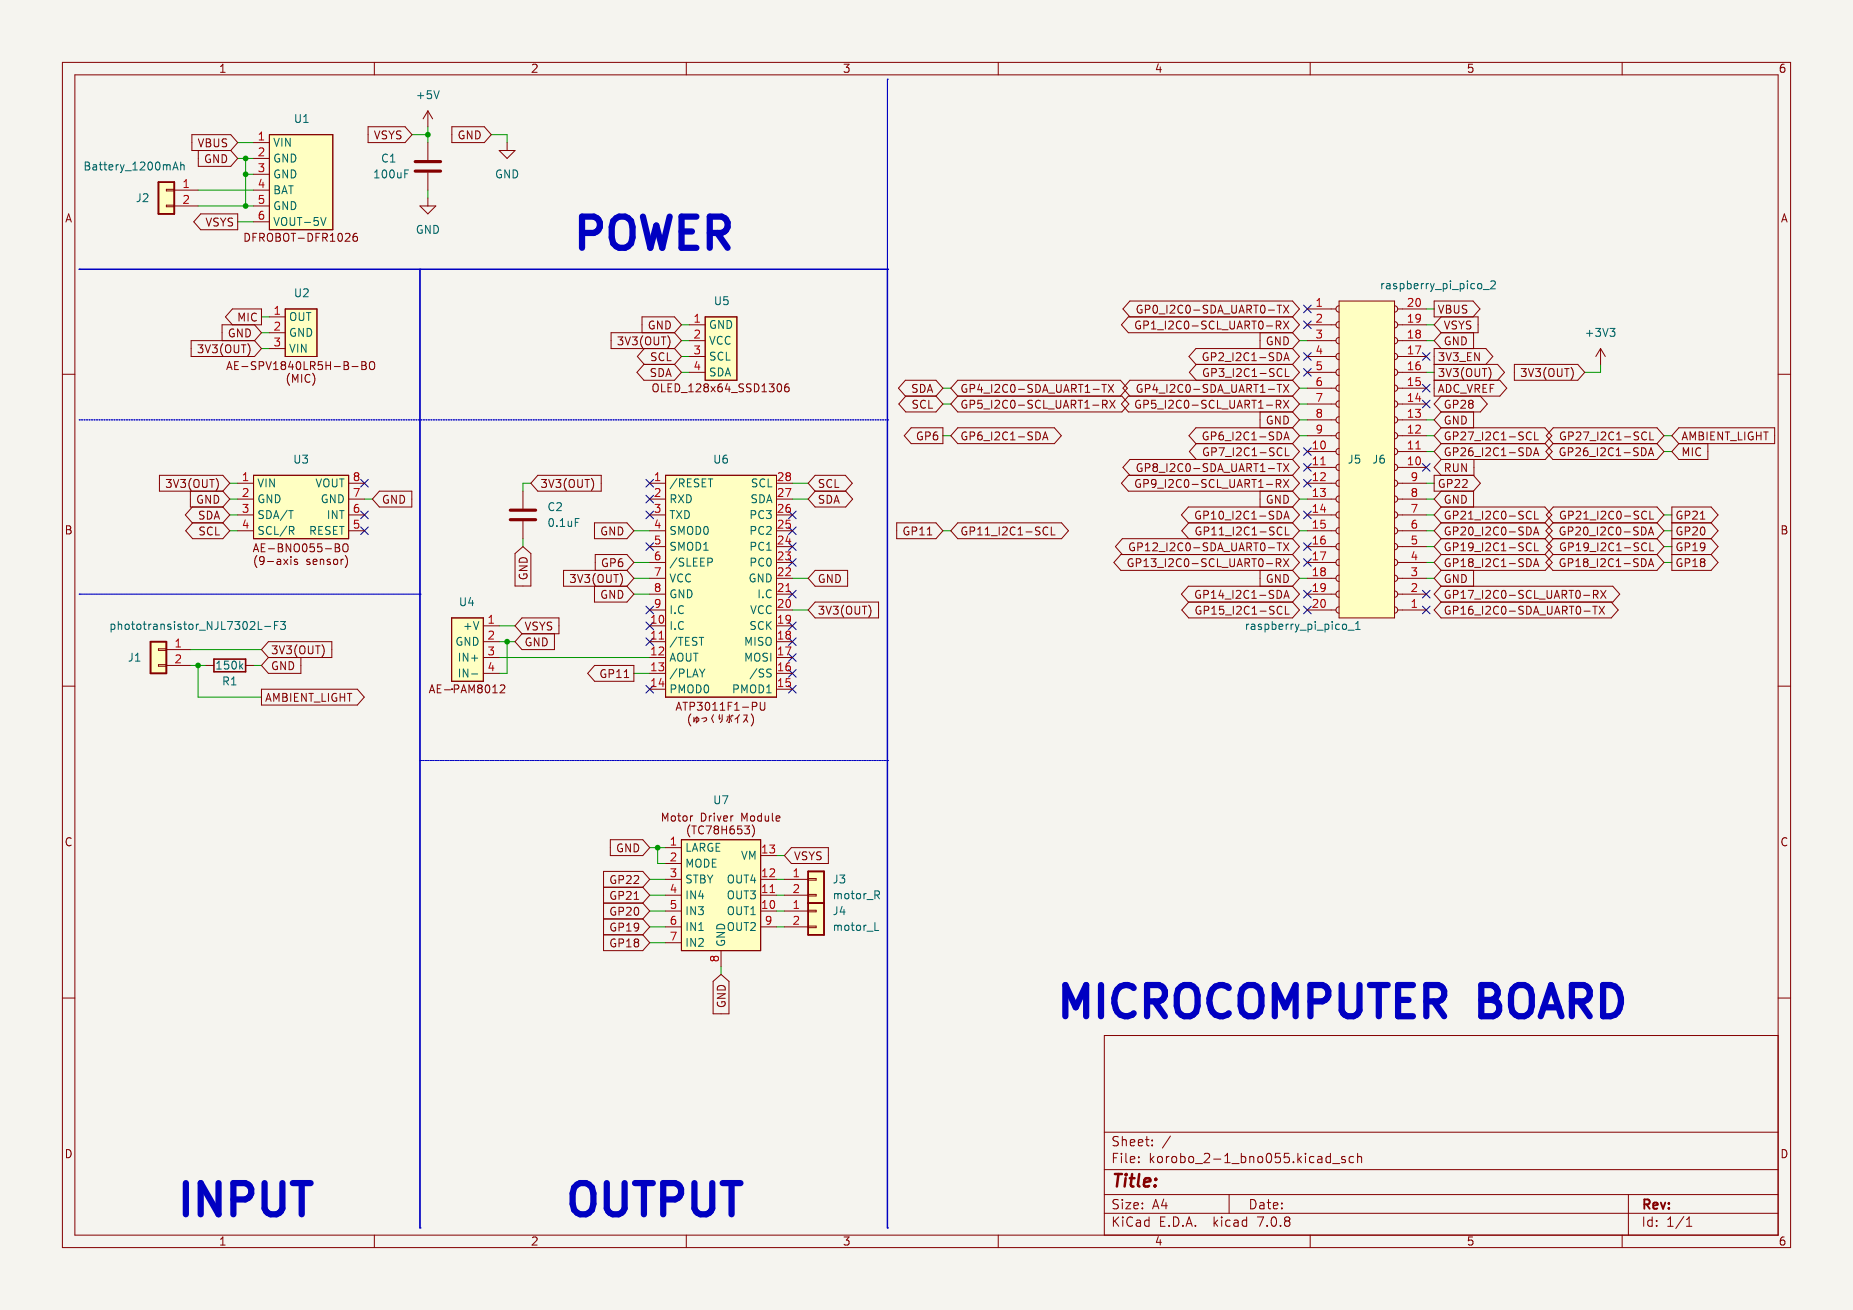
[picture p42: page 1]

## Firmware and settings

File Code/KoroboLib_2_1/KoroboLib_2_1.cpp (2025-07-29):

#include "KoroboLib_2_1.h"

// 9-axis sensor
Adafruit_BNO055 bno = Adafruit_BNO055(-1, 0x28, &Wire);
// OLED
Adafruit_SSD1306 oled(128, 64, &Wire, -1);

KoroboLib_2_1::KoroboLib_2_1() {

}

KoroboLib_2_1::~KoroboLib_2_1() {

}

void KoroboLib_2_1::begin(unsigned int motor_select){
  motor_val = motor_select;

  Wire.begin();
  delay(10);

  bno.begin();
  delay(10);

  oled.begin(SSD1306_SWITCHCAPVCC, 0x3C);
  delay(10);
  oled.setTextColor(SSD1306_WHITE);
  oled.clearDisplay();
  oled.display();
  delay(10);

  pinMode(USB_POWER_PIN, INPUT);

  switch (motor_val) {
  case OLD:
    motor_in4_pin = MOTOR_IN4_OLD_PIN;
    motor_in3_pin = MOTOR_IN3_OLD_PIN;
    motor_in1_pin = MOTOR_IN1_OLD_PIN;
    motor_in2_pin = MOTOR_IN2_OLD_PIN;
    motor_en_pin = MOTOR_EN_OLD_PIN;
    break;
  case TC:
    motor_in4_pin = MOTOR_IN4_T_PIN;
    motor_in3_pin = MOTOR_IN3_T_PIN;
    motor_in1_pin = MOTOR_IN1_T_PIN;
    motor_in2_pin = MOTOR_IN2_T_PIN;
    motor_en_pin = MOTOR_EN_T_PIN;
    pinMode(MOTOR_MODE_T_PIN, OUTPUT);
    digitalWrite(MOTOR_MODE_T_PIN, LOW);
    break;
  case DRV:
    motor_in4_pin = MOTOR_IN4_D_PIN;
    motor_in3_pin = MOTOR_IN3_D_PIN;
    motor_in1_pin = MOTOR_IN1_D_PIN;
    motor_in2_pin = MOTOR_IN2_D_PIN;
    motor_en_pin = MOTOR_EN_D_PIN;
    pinMode(MOTOR_MODE_D_PIN, OUTPUT);
    digitalWrite(MOTOR_MODE_D_PIN, LOW);
    break;
  default:
    break;
  }

  pinMode(motor_in4_pin, OUTPUT);
  pinMode(motor_in3_pin, OUTPUT);
  pinMode(motor_in1_pin, OUTPUT);
  pinMode(motor_in2_pin, OUTPUT);
  pinMode(motor_en_pin, OUTPUT);

  pinMode(VOICE_EN_PIN, OUTPUT);
  pinMode(VOICE_STATE_PIN, INPUT);

  delay(10);
}

void KoroboLib_2_1::Imu_getData(){
  korobo_acc_temp = korobo_acc;
  korobo_gyro_temp = korobo_gyro;
  korobo_mag_temp = korobo_mag;
  korobo_acc = bno.getVector(Adafruit_BNO055::VECTOR_ACCELEROMETER);
  korobo_gyro = bno.getVector(Adafruit_BNO055::VECTOR_GYROSCOPE);
  korobo_mag = bno.getVector(Adafruit_BNO055::VECTOR_MAGNETOMETER);
}

int KoroboLib_2_1::AmbientLight_getData(){
  return analogRead(AMBIENT_LIGHT_PIN);
}

int KoroboLib_2_1::Mic_getData(){
  return abs(analogRead(MIC_PIN));
}

int KoroboLib_2_1::_SoundAmplitude(int data) {
  if (mic_val_temp != 0) {
    if (data - mic_val_temp >= 0) {
      if (mic_val_positive != true) {
        mic_val_min = mic_val_temp;
        mic_count++;
      }
      mic_val_positive = true;
    } 
    else {
      if (mic_val_positive != true) {
        mic_val_max = mic_val_temp;
        mic_count++;
      }
      mic_val_positive = false;
    }
    mic_val_temp = data;
  } else mic_val_temp = data;

  if (mic_count == 2) {
    mic_ans = mic_val_max - mic_val_min;
    mic_count = 0;
  }

  return mic_ans;
}

void KoroboLib_2_1::_Eye_point_size_init(){
  dX_point = 0;
  dY_point = 0;
  dX_size = 0;
  dY_size = 0;
}

void KoroboLib_2_1::_Eye_sound() {
  int eye_sound;
  int sound_amp = _SoundAmplitude(Mic_getData());
  eye_sound = abs(sound_amp - sound_amp_temp);
  sound_amp_temp = sound_amp;
  //RC-Filter
  eye_sound = round((1 - RC_FILTER) * eye_sound + RC_FILTER * eye_sound_temp);
  eye_sound_temp = eye_sound;
  eye_sound -= 3;

  //目の横幅反映
  int eye_sound_x_limit = 12;
  if (eye_sound > eye_sound_x_limit) {
    dX_point -= eye_sound_x_limit / 2;
    dX_size += eye_sound_x_limit;
  }
  else {
    dX_point -= eye_sound / 2;
    dX_size += eye_sound;
  }
  //目の縦幅反映
  int eye_sound_y_limit = 24;
  eye_sound *= 2;
  if (EYE_HEIGHT + dY_size - eye_sound > 4 || EYE_HEIGHT + dY_size - eye_sound_y_limit > 4) {
    if (eye_sound > eye_sound_y_limit) {
      dY_point += eye_sound_y_limit / 2;
      dY_size -= eye_sound_y_limit;
    }
    else {
      dY_point += eye_sound / 2;
      dY_size -= eye_sound;
    }
  }
}

void KoroboLib_2_1::_Eye_imu() {
  Imu_getData();
  int eye_agx, eye_agy;
  eye_agx = round((korobo_acc.x() - korobo_acc_temp.x()) * 100 + (korobo_gyro.z() - korobo_gyro_temp.z()) * 0.5);
  eye_agy = round((korobo_acc.z() - korobo_acc_temp.z()) * 100 + (korobo_gyro.x() - korobo_gyro_temp.x()) * 1);
  //RC-Filter
  eye_agx = round((1 - RC_FILTER) * eye_agx + RC_FILTER * eye_agx_temp);
  eye_agy = round((1 - RC_FILTER) * eye_agy + RC_FILTER * eye_agy_temp);
  eye_agx_temp = eye_agx;
  eye_agy_temp = eye_agy;

  ///*
  for (int n = 0; n < EYE_AG_FILTER - 1; n++) {
    Eye_agx_array[n] = Eye_agx_array[n + 1];
    Eye_agy_array[n] = Eye_agy_array[n + 1];
  }
  Eye_agx_array[EYE_AG_FILTER - 1] = eye_agx;
  Eye_agy_array[EYE_AG_FILTER - 1] = eye_agy;

  eye_agx = 0;
  eye_agy = 0;
  for (int n = 0; n < EYE_AG_FILTER; n++) {
    eye_agx += Eye_agx_array[n];
    eye_agy += Eye_agy_array[n];
  }
  eye_agx = eye_agx / EYE_AG_FILTER;
  eye_agy = eye_agy / EYE_AG_FILTER;
  //*/

  int eye_agx_limit = 10;
  if (eye_agx > eye_agx_limit) dX_point += eye_agx_limit;
  else if (eye_agx < -eye_agx_limit) dX_point += -eye_agx_limit;
  else dX_point += eye_agx;

  int eye_agy_limit = 5;
  if (eye_agy > eye_agy_limit) dY_point += eye_agy_limit;
  else if (eye_agy < -eye_agy_limit) dY_point += -eye_agy_limit;
  else dY_point += eye_agy;
}

void KoroboLib_2_1::_Eye_light() {
  int eye_al_val = AmbientLight_getData();
  int eye_al_val_ave = 0;
  int eye_al_dx, eye_al_dy;
  //RC-Filter
  eye_al_val = (1 - RC_FILTER) * eye_al_val + RC_FILTER * eye_al_val_temp;
  //Average-Filter
  for (int i = FILTER_SAMPLE - 1; i > 0; i--) Eye_al_array[i] = Eye_al_array[i - 1];
  Eye_al_array[0] = eye_al_val;
  for (int i = 0; i < FILTER_SAMPLE; i++) eye_al_val_ave += Eye_al_array[i];
  eye_al_val_ave /= FILTER_SAMPLE;

  eye_al_dx = abs(round((eye_al_val - eye_al_val_ave) * 0.03));
  eye_al_dy = abs(round((eye_al_val_ave - eye_al_val) * 0.05));

  dX_size += eye_al_dx;
  dX_point -= eye_al_dx / 2;
  dY_size -= eye_al_dy;
  dY_point += eye_al_dy / 2;

  eye_al_val_temp = eye_al_val;
}

void KoroboLib_2_1::_Eye(){
  oled.clearDisplay();

  oled.fillRect(X_EYE_L + dX_point, Y_EYE + dY_point, EYE_WIDTH + dX_size, EYE_HEIGHT + dY_size, WHITE);
  oled.fillRect(X_EYE_R + dX_point, Y_EYE + dY_point, EYE_WIDTH + dX_size, EYE_HEIGHT + dY_size, WHITE);

  oled.display();
}

void KoroboLib_2_1::Eye(unsigned int num) {
  _Eye_point_size_init();
  //mode select
  if (num % SOUND == 0) _Eye_sound();
  if (num % IMU == 0) _Eye_imu();
  if (num % LIGHT == 0) _Eye_light();

  _Eye();
}

void KoroboLib_2_1::Eye(int dX_point_u, int dY_point_u, int dX_size_u, int dY_size_u) {
  dX_point = dX_point_u;
  dY_point = dY_point_u;
  dX_size = dX_size_u;
  dY_size = dY_size_u;

  _Eye();
}

void KoroboLib_2_1::Eye(int dX_point_u, int dY_point_u, int dX_size_u, int dY_size_u, unsigned int num) {
  _Eye_point_size_init();
  //mode select
  if (num % 2 == 0) _Eye_sound();
  if (num % 3 == 0) _Eye_imu();
  if (num % 5 == 0) _Eye_light();

  dX_point += dX_point_u;
  dY_point += dY_point_u;
  dX_size += dX_size_u;
  dY_size += dY_size_u;

  _Eye();
}
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

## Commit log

2025-04-09 file name change
    [cover_b_2-1.stl, cover_t_2-1.stl]
2025-04-09 file name change. And README update.
    [cover_stopper.stl]
2025-04-09 schematic add
2025-04-16 TAMIYA GearBox Quantity mistake.
2025-04-18 3mf-file add
    [korobo_2-1_PLA.3mf]
2025-04-21 ambient-light sensor -> eye-move
2025-04-30 update: Model...wheel_t_shaft
    [wheel_t2.stl, wheel_t_shaft.stl]
2025-05-01 update: Model...wheel_t and wheel_t_shaft
    [korobo_2-1_PLA.3mf, wheel_t.stl, wheel_t_shaft.stl]
2025-05-02 update: Code...KoroboLib, Disable motor upon USB connection.
2025-05-02 update: Model...wheel_b_2-1.stl & add: Model...STEP-Files
    [cover_b_2-1.step, cover_stopper.step, cover_t_2-1.step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]
2025-05-03 update: Model...wheel_b_2-1.stl/.step
    [wheel_b_2-1.step, wheel_b_2-1.stl]
2025-05-04 update: Model...wheel_b_2-1.stl/step
    [wheel_b_2-1.step, wheel_b_2-1.stl]
2025-05-04 add: Model...3mf files
    [korobo_2-1_PLA.3mf, korobo_2-1_TPU.3mf]
2025-05-07 update: Model...cover_stopper.stl/step
    [cover_stopper.step, cover_stopper.stl]
2025-05-08 update: Model...wheel_t_shaft.stl/step
    [wheel_t_shaft.step, wheel_t_shaft.stl]
2025-05-08 update: Model...korobo_2-1_PLA/TPU.3mf
    [korobo_2-1_PLA.3mf, korobo_2-1_TPU.3mf]
2025-05-09 add: Document...wire_parts.jpg
2025-05-12 update: Code...change board-manager to arduino-pico, update PI-Control
2025-05-24 update: Code...KoroboLib_2_1 >> Motor(), _Motor()..
2025-06-16 update: Board...main board version-up!
2025-07-10 update: Code...KoroboLib_2_1, main-board ver.3.2 supported. test
2025-07-15 update: Code...KoroboLib ver. 2.0, supported main-board ver. 3.2
    [korobo_2-1_PLA.3mf]
2025-07-29 update: Code...mind_2-1.ino >> comment mistake
    [mind_2-1.ino]
2025-07-30 add: Document...main-board image files
2025-10-09 update:PLA parts 3mf-file
    [korobo_2-1_PLA.3mf]
2025-10-10 update: Model...PLA-parts 3mf-file
    [korobo_2-1_PLA.3mf]
2025-10-10 update: Model...Directory name STL -> STL(OLD)
    [cover_b_2-1.stl, cover_stopper.stl, cover_t_2-1.stl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]
2025-10-12 update: README.md, add: Document...motor unit GIF
2025-10-13 update: README.md, add: Document...wire making GIF
2025-10-14 update: Board...README.md image size-up
2026-05-05 update: README.md, 学生という記載を削除しました（新社会人になりました！）
2026-05-06 update: README.md, ギアボックスの説明追記
2026-05-06 update: README.md, ぶんぽう
2026-05-06 update: README.md, 文法修正
2026-05-06 update: README.md, Main-Board ついき
2026-05-31 delete: Model->2-1Gen_KOROBO.step
    [2-1Gen_KOROBO.step]
2026-05-31 update: Model->cover_t_2-1.step, ディスプレイモジュールの負荷軽減and USB差込口の改善
    [cover_t_2-1.step]
